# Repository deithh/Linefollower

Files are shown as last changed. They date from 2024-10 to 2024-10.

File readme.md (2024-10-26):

# Line Follower Robot  

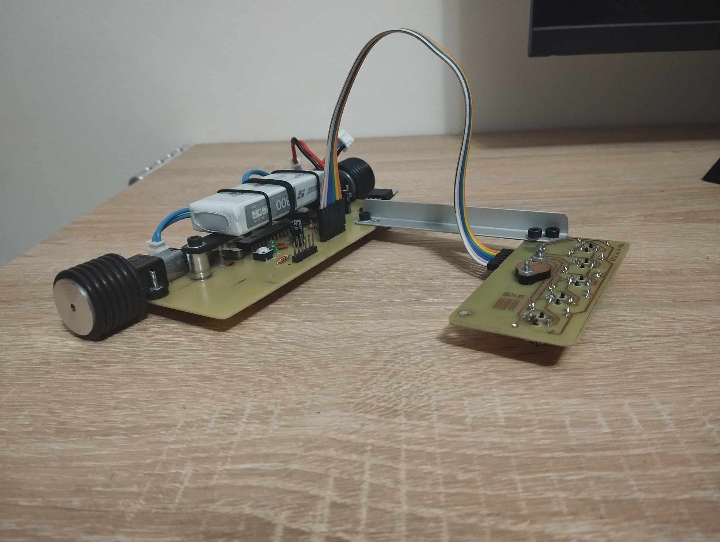
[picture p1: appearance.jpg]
appearance
  

## Overview  
This repository contains the project of a Line Follower Robot developed as part of the Computer Systems Architecture course at the Poznan University of Technology. The robot is designed to autonomously follow a black line on a flat surface using embedded sensors and self-developed control logic. The project involved designing, assembling, and programming the robot from scratch.  

**We managed to create an autonomous system that can follow the line at a speed of approximately 0.6 m/s**  
We won a competition outperforming 10 other teams with our creation of a lightweight robot featuring an efficient drive system.  

## Team Members  
1. Hubert Błaszczyk - 155085
- PCB etching
- Software development
- Video production
- System testing and calibration

2. Bartosz Operacz - 155957
- PCB etching
- Software development
- Documentation preparation
- System testing and calibration

3. **I was responible for:**
- PCB etching
- Robot design
- Component assembly
- System testing and calibration  

## Project Goal
The objective of the project was to develop a robot capable of autonomously tracking a black line by:

- Detecting a black line beneath it  
- Operating on a flat surface with the ability to steer and adjust speed  
- Being self-powered  
- Generating signals to follow the line accurately  
- Indicating correct operation through LEDs  
- Allowing easy reprogramming for improvements or troubleshooting  

## Technical Specifications
- Sensors: 5 TCRT5000 optical sensors to detect line position.
- Motors: 2 N20-BT16 motors with 2000 rpm, allowing ~2 m/s speed.
- Motor Driver: TB6612FNG for dual-channel motor control.
- Power Source: 2S 7.4V Li-Pol battery.
- Voltage Regulator: LM7805 with reverse current protection.
- Microcontroller: ATMEGA328P-PN, 16MHz clock.
- Other Features: Custom PCB with solder mask, LED indicators, programmable SPI interface.

## Software Overview
The software was developed to:  

Read sensor signals to determine the robot's position relative to the line.
Control motor speed and direction based on a PID (Proportional-Integral-Derivative) controller.
Use LEDs to signal operational status and low battery levels.
Key Functions:

drive_motors: Controls motor speed and direction.
calibrate: Calibrates the sensors for line detection.
calculate_error: Calculates deviation from the line.
PID control: Adjusts motor speed to correct positioning.
Assembly and Etching
The PCB etching process was completed in-house, following these steps:

Preparing film layouts.
UV exposure and etching.
Drilling and mounting components.
Final soldering and assembly.

## Budget Summary
The total cost for the project components was approximately 404.53 PLN.

## Demo Video
A video demonstration of the Line Follower Robot is available on YouTube:  
[result](https://youtu.be/YW8YQgWOzjk)  
[project video](https://www.youtube.com/watch?v=wPkWPQ8s4SI&ab_channel=NapewnonieHubert)  

## Notes
Capacitor C5 was removed due to programming issues.  
The footprint for LM7805 was incorrectly sized, requiring adjustments.

### Project documentation is available in polish

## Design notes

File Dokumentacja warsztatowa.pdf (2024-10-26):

INSTYTUT INFORMATYKI
WYDZIAL INFORMATYKI I TELEKOMUNIKACJI, POLITECHNIKA POZNANSKA

## ARCHITEKTURA SYSTEMÓW KOMPUTEROWYCH 2024

prowadzący: dr inż. RAFAŁ KLAUS

## Line Follower

### drużyna warsztatowa nr 8

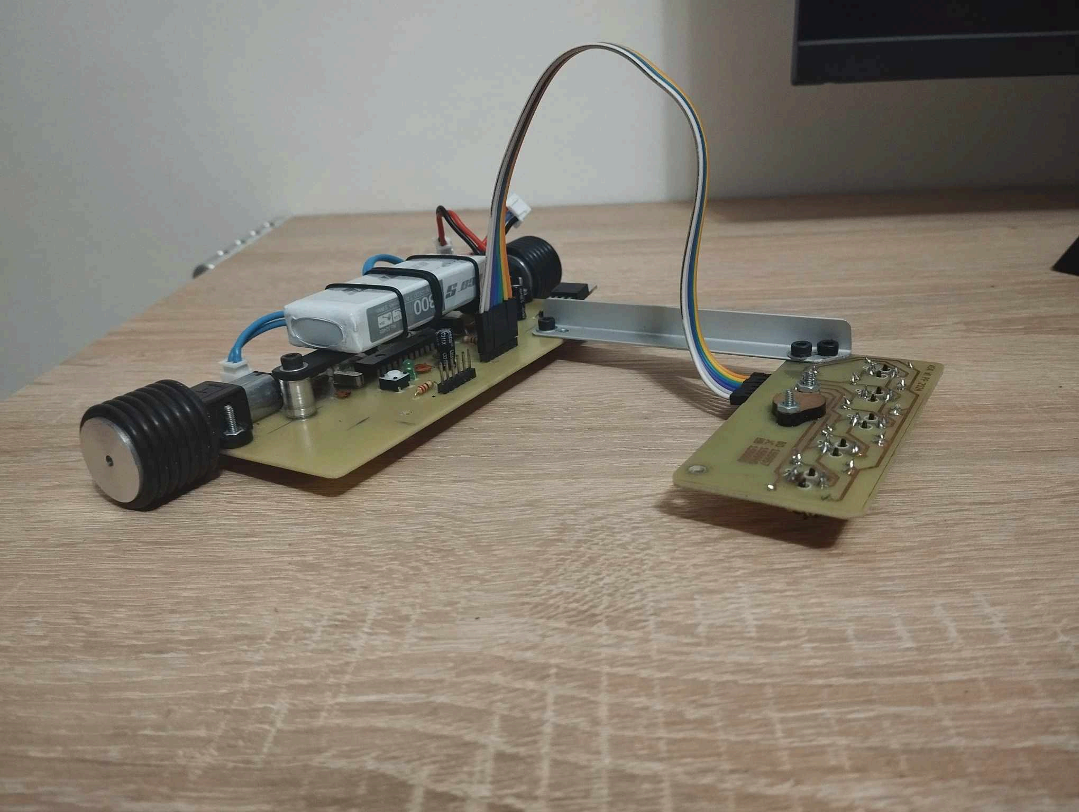
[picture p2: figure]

Lp. | Autorzy | Indeks | nr grupy dziekańskiej | Zadania
1 | Hubert Błaszczyk | 155085 | 6 | 1. Wytrawienie płyt 2. Realizacja oprogramowania 3. Wykonanie filmu 4. Testowanie i trymowanie systemu
2 | Jan Cieśla | 155945 | 4 | 1. Wytrawienie płyt 2. Projekt robota 3. Montaż komponentów 4. Testowanie i trymowanie systemu
3 | Bartosz Operacz | 155957 | 1 | 1. Wytrawienie płyt 2. Realizacja oprogramowania 3. Przygotowanie dokumentacji 4. Testowanie i trymowanie systemu

Poznań, 2024

# Wprowadzenie

Celem naszej drużyny było własnoręczne stworzenie robota typu LineFollower, którego zadaniem jest podążanie po znajdującej się na podłodze czarnej linii.
Pomysł zakłada że robot powinien:
- wykrywać znajdującą się pod nim linię,
- mieć możliwość poruszania się po płaskiej powierzchni, skręcania
- posiadać własne zasilanie,
- generować odpowiednie sygnały umożliwiające podążanie za linią,
- móc informować o jego prawidłowym funkcjonowaniu,
- mieć możliwość łatwego programowania z zewnątrz.

# Rozwiązania techniczne

W robocie zastosowano:
- 5 transoptorów odbiciowych TCRT5000 aby wykrywać czarną linię. Zastosowane ze względu na wysoki dystans działania.
- 2 silniki N20-BT16 służące za napęd, połączone bezpośrednio do kół robota pozbywając się w ten sposób problemów związanych z przenoszeniem napędu, jednocześnie realizując skręt. 2000 rpm pozwala na jazdę z prędkością ok 2m/s przy zastosowanych przez nas kołach fi24mm, zapewniając zadowalające przyspieszenie.
- dwukanałowy sterownik silników TB6612FNG umożliwiający sterowanie silnikami,
- pakiet Li-Pol 2S 7.4V 20C Dualsky 800mAh - zasilanie robota. Dobrane ze względu na dobry stosunek wagi do pojemności oraz możliwość dostarczenia prądu o dużym natężeniu.
- stabilizator napięcia LM7805 wraz z układem zabezpieczenia przed prądem zwrotnym,
- mikrokontroler ATMEGA328P-PN taktowany oscylatorem 16MHz,
- dzielnik napięcia aby umożliwić pomiar napięcia pakietu i wykrycie gdy jest on zbyt niski,
- 2 diody led oraz przycisk w celu umożliwienia komunikacji człowiek-robot,
- wyprowadzony interfejs spi służący do programowania robota.
- zabezpieczenie przed odwrotnym podłączeniem zasilania w postaci asymetrycznego gniazda zasilania
- Filtracja zasilania dla układów scalonych, układ zaprojektowany z troską o minimalizację zakłóceń

## Opis konstrukcji robota

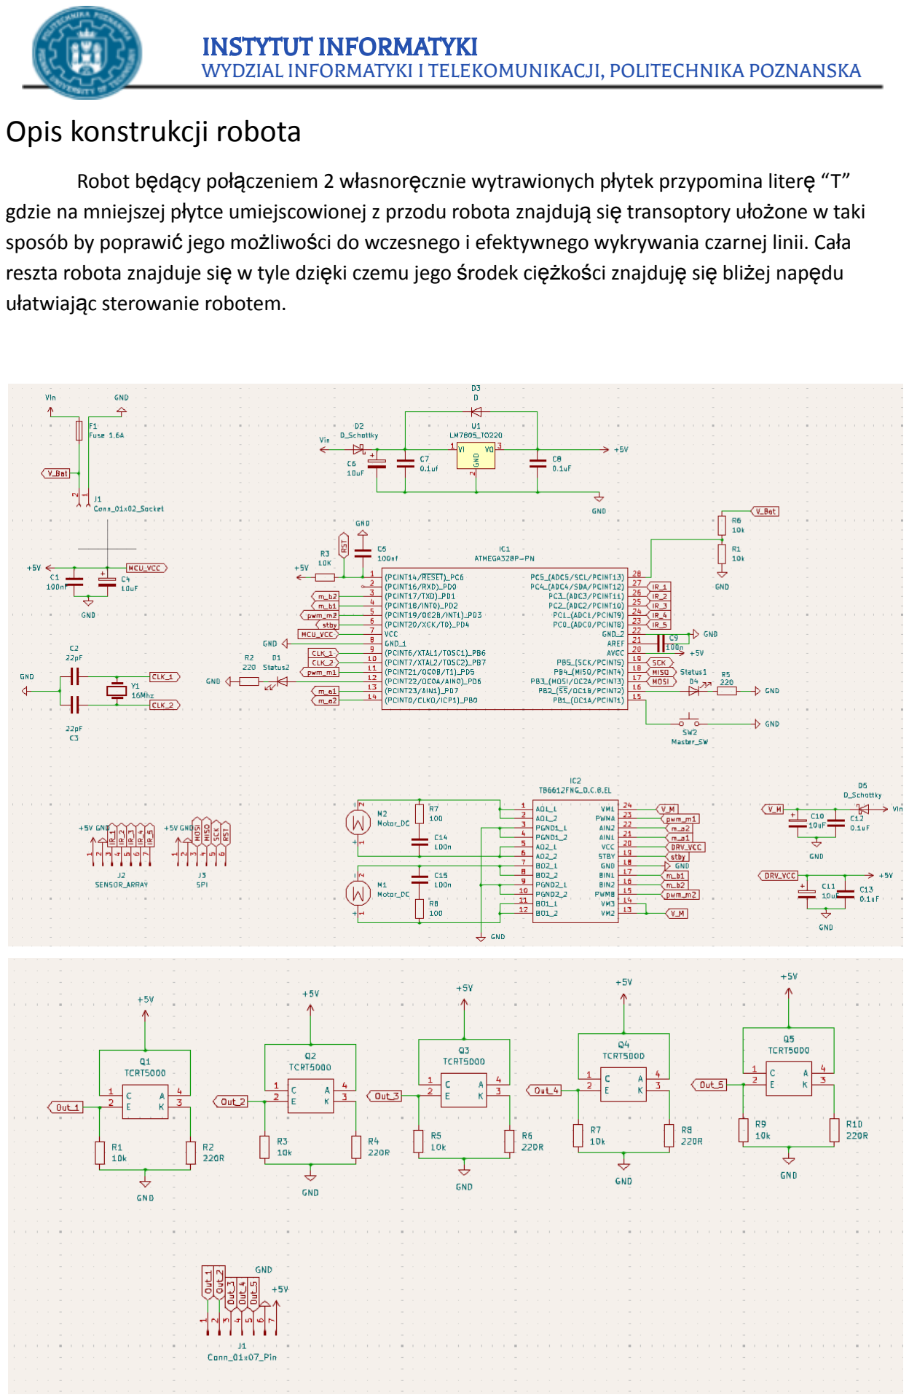
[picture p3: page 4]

Robot będący połączeniem 2 własnoręcznie wytrawionych płytek przypomina literę “T” gdzie na mniejszej płytce umiejscowionej z przodu robota znajdują się transoptory ułożone w taki sposób by poprawić jego możliwości do wczesnego i efektywnego wykrywania czarnej linii. Cała reszta robota znajduje się w tyle dzięki czemu jego środek ciężkości znajduję się bliżej napędu ułatwiając sterowanie robotem.

# Schematy i opis

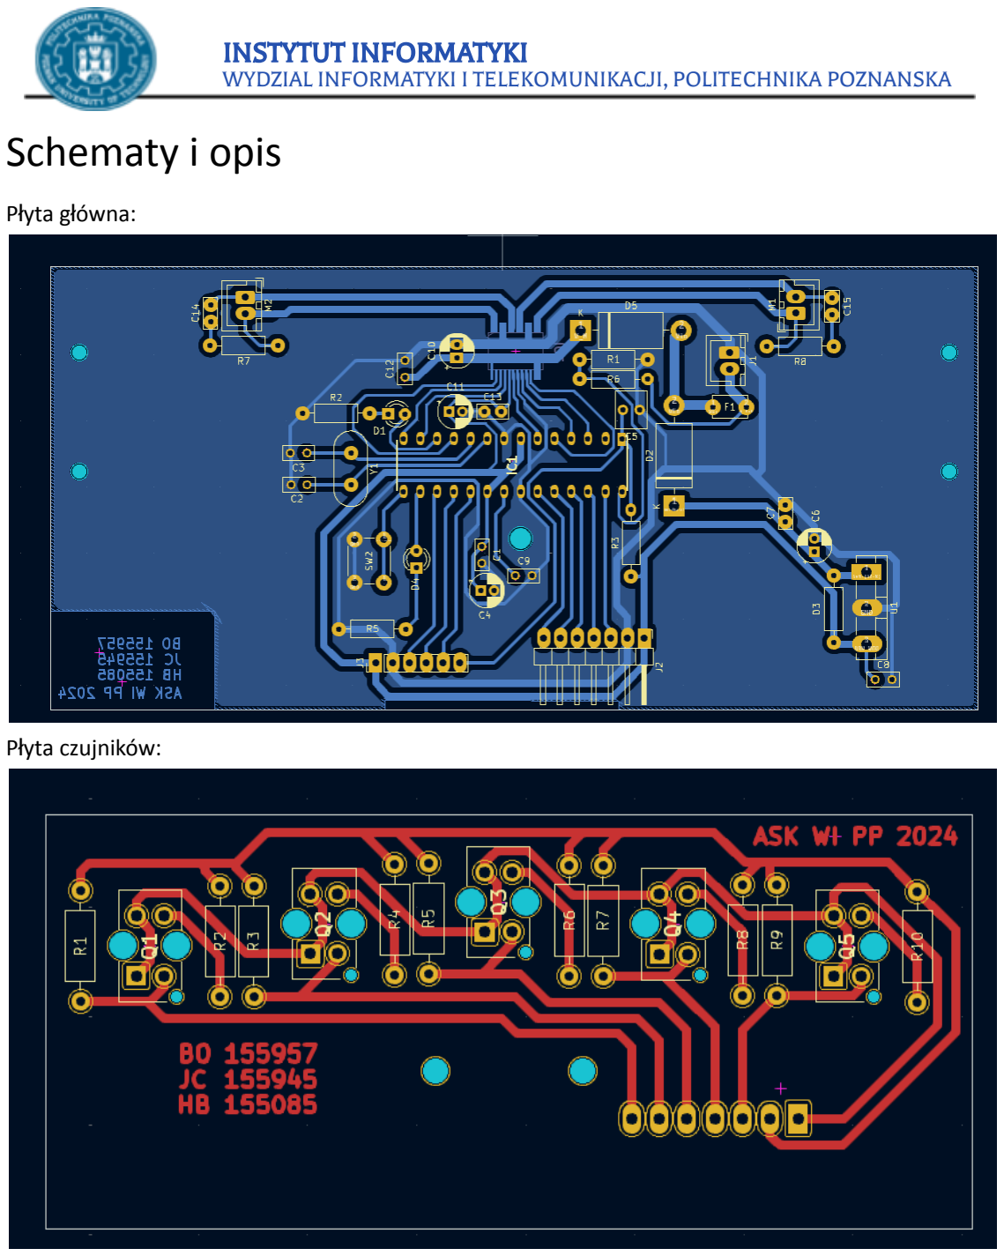
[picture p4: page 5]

Płyta główna:

Płyta czujników:

## Opis trawienia:

- Przygotowanie klisz - wydruk layout’u na kalce technicznej lub przezroczystej folii. W celu ograniczenia transparentności klisz połączyliśmy dwie naraz, wymagane jest precyzyjne ustawienie z pomocą znaków ustalających na wydrukach.
- Przygotowanie ciemni (żółte / czerwone światło), roztworów wywoływacza uniwersalnego w proporcji 5.5g/100ml i nadsiarczanu sodu 20g/100ml oraz laminatu z fotorezystem pozytywowym dociętym ok 5mm nad wymiar, należy ogratować krawędzie laminatu. Wywoływacz w temperaturze pokojowej, wytrawiacz należy podgrzać w kąpieli wodnej do ok 50 stopni.
- Zdjęcie folii ochronnej z laminatu, ustawienie kliszy (klisza nie odbita lustrzanie, tonerem do laminatu).
- Naświetlenie płyty światłem UV przez eksperymentalnie dobrany czas (w naszym przypadku 180s). Należy zwrócić uwagę na notę katalogową laminatu i długość fali emitowaną przez naszą lampe, w naszym przypadku duża lampa do paznokci spełniła swoje zadanie. Podczas naświetlania wymagany jest docisk kliszy do laminatu aby uniknąć wybrzuszania się kliszy. (Do przygotowania małego PCB wystarczyła nam ciężka szyba, w przypadku płyty głównej posłużyliśmy się workiem próżniowym i ciśnieniem atmosfery)
- Wywoływanie ok 150-180s w roztworze o temperaturze pokojowej, wymagane mieszanie. Po wyjęciu płytkę należy wypłukać. Za krótko wywoływany rezyst nie dopuści do poprawnego wytrawiania się PCB.
- Wytrawianie ok 10-20min w zależności od rozmiaru płyty i świeżości roztworu, wymagane utrzymywanie b327 w podwyższonej temperaturze. Trawimy do momentu zaniku 100% miedzi z przestrzeni między ścieżkami. Po wyjęciu płytkę należy wypłukać.
- Zmycie pozostałego rezystu acetonem, obcięcie nadwymiarowego laminatu piłą włośnicową.
- Zabezpieczenie PCB lakierem / soldermaską.

# Oprogramowanie

W celu zapewnienia odpowiedniego sposobu działania robota wymagane było napisanie oprogramowania, którego zadaniem było odczytywanie wartości sygnałów zwracanych przez transoptory odbiciowe i na ich podstawie generowanie odpowiednich sygnałów do sterownika silników aby robot poruszał się zgodnie z czarną linią.

## Wykorzystane biblioteki

W programie skorzystano z biblioteki TB6612 SparkFun ułatwiającej sterowanie silnikami.

Znajdujące się w niej klasa, metody, i procedury, które zostały użyte w programie to:
- klasa Motor

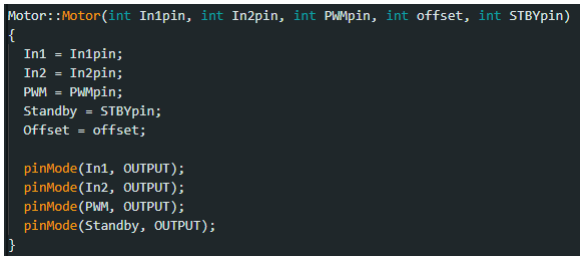
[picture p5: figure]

- drive (wykorzystywana do poruszania konkretnym silnikiem)

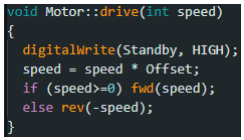
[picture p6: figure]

- fwd

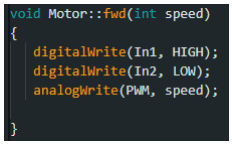
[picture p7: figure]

- rev

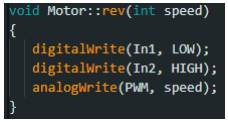
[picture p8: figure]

- procedura brake (wykorzystywana do hamowania obu silników)
- metoda brake

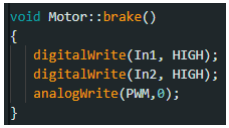
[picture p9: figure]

## Zdefiniowane stałe

Dla ułatwienia i zwiększenia czytelności zdefiniowano makra zastępujące identyfikatory odpowiednimi numerami pinów i innych pomocniczych stałych.

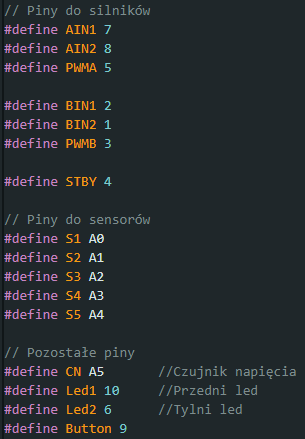
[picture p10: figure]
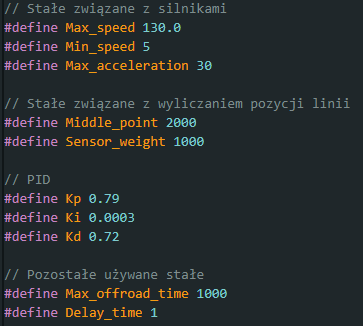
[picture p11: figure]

## Wykorzystane funkcje

Na potrzeby programu zdefiniowano kilka makr, procedur i funkcji pomocniczych:
- sbi i cbi (wykorzystywane do ustawiania konkretnych bitów rejestrów sfr)

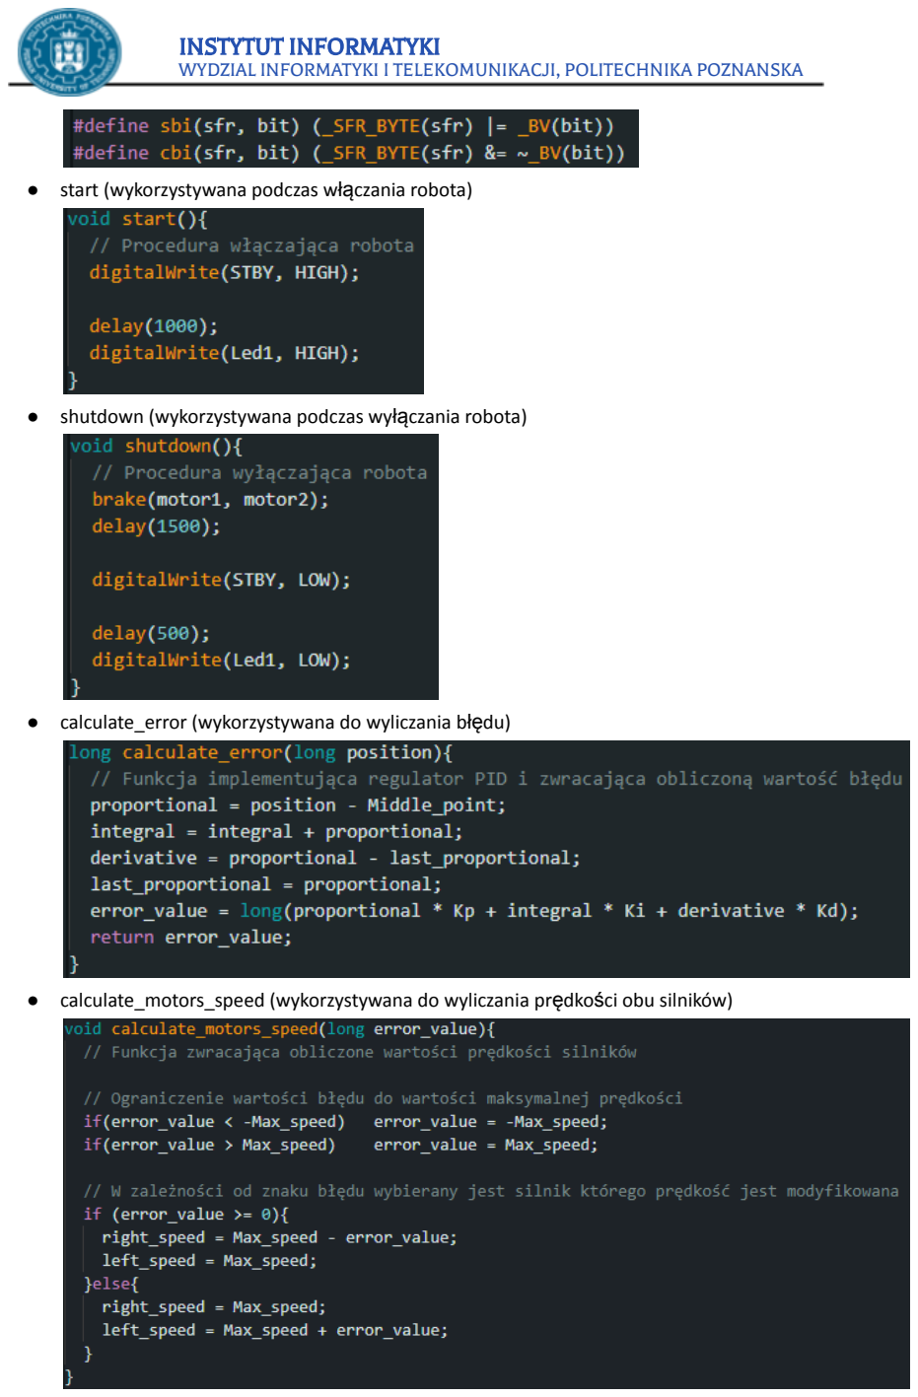
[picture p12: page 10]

- start (wykorzystywana podczas włączania robota)
- shutdown (wykorzystywana podczas wyłączania robota)
- calculate_error (wykorzystywana do wyliczania błędu)
- calculate_motors_speed (wykorzystywana do wyliczania prędkości obu silników)

- drive_motors (wykorzystywana do sterowania silnikami)

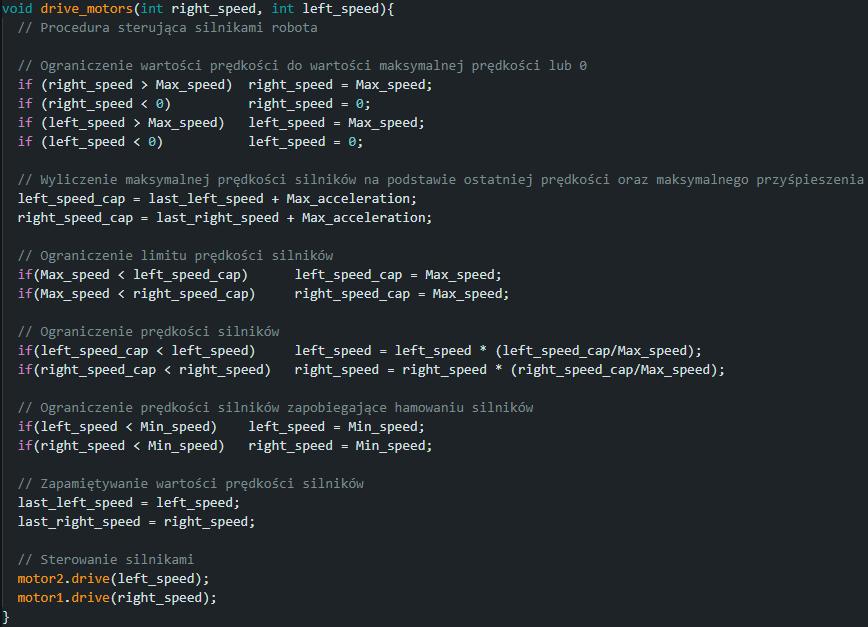
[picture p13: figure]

- calibrate (wykorzystywana do kalibracji sensorów)

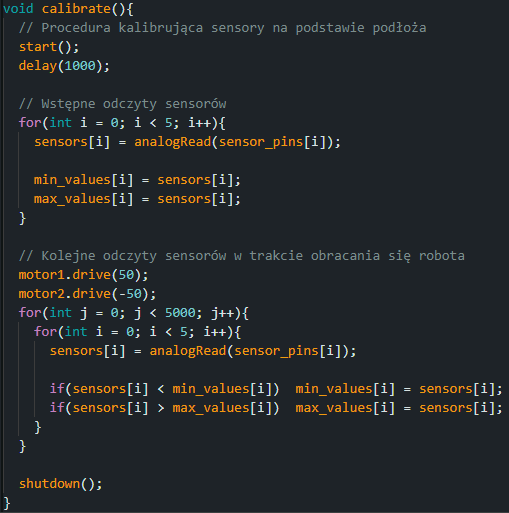
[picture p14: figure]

## Deklaracja i inicjalizacja zmiennych

Na początku programu są deklarowane i inicjalizowane wszystkie zmienne wymagane do poprawnego działania programu.

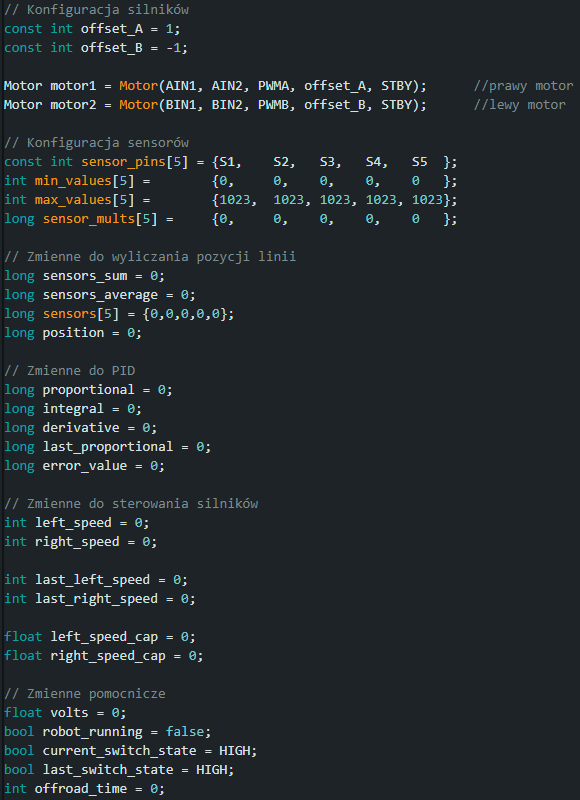
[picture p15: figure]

## Przygotowanie mikrokontrolera do działania

Następnie dokonywana jest:
- konfiguracja,

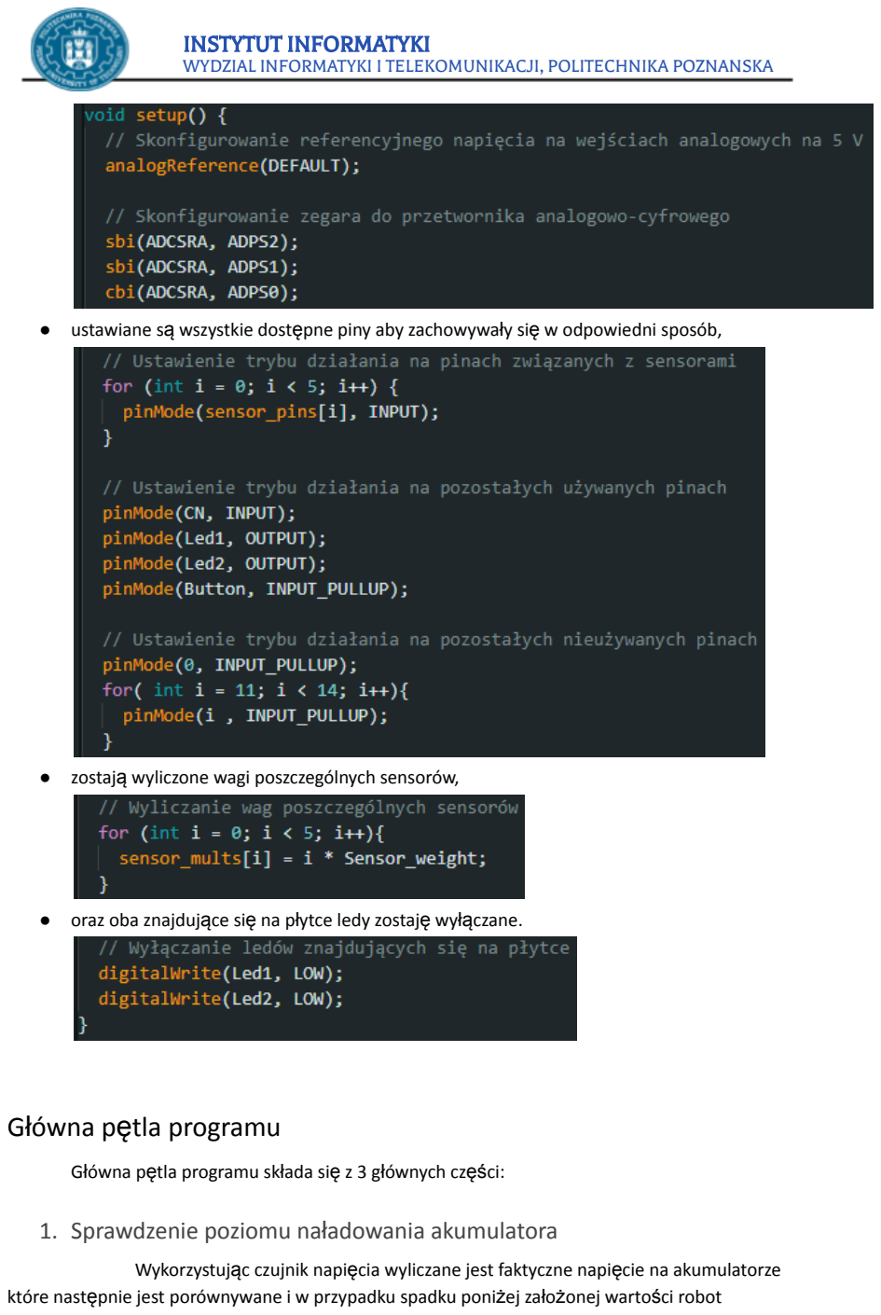
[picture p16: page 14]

- ustawiane są wszystkie dostępne piny aby zachowywały się w odpowiedni sposób,
- zostają wyliczone wagi poszczególnych sensorów,
- oraz oba znajdujące się na płytce ledy zostaję wyłączane.

## Główna pętla programu

Główna pętla programu składa się z 3 głównych części:

### 1. Sprawdzenie poziomu naładowania akumulatora

Wykorzystując czujnik napięcia wyliczane jest faktyczne napięcie na akumulatorze które następnie jest porównywane i w przypadku spadku poniżej założonej wartości robot odpowiednio informuje zapalając odpowiednią diodę, lub w przypadku jeszcze większego odchyłu napięcia program zatrzyma działanie i nie pozwoli na ponowne uruchomienie robota jednocześnie informując o krytycznym poziomie akumulatora migającą diodą led.

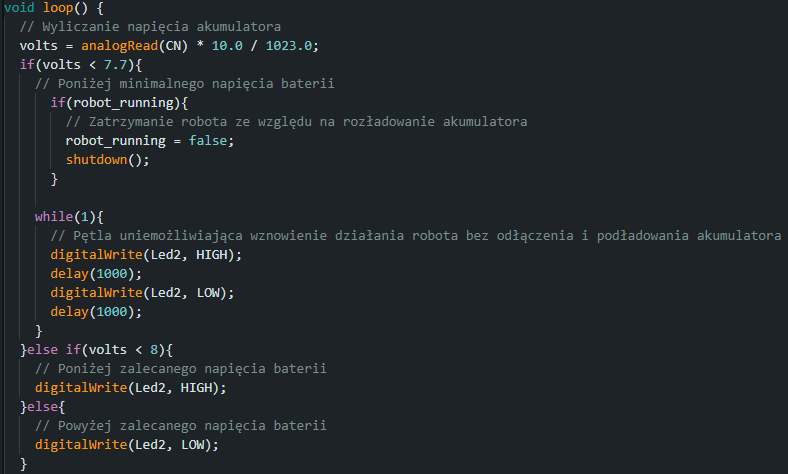
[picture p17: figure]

### 2. Sekcja związana z przyciskiem

Za pomocą zmiennej przechowującej ostatni stan przycisku jest możliwe wyłapanie przez program momentu jednokrotnego naciśnięcia przycisku a przez powtórne sprawdzenie stanu przycisku możliwe jest rozróżnienie krótszego i dłuższego przytrzymania przycisku dzięki czemu można wybrać czy robot powinien zacząć kalibrację lub odpowiednio zostać włączony lub wyłączony zależnie od jego aktualnego stanu (w trakcie działania robota kalibracja jest niemożliwa). O aktualnym stanie robota informuje dioda led umieszczona w tylnej części robota.

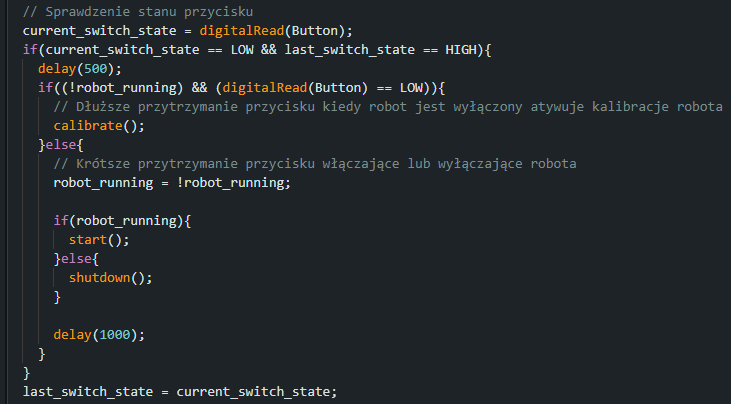
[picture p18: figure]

### 3. Sekcja związana z jazdą po linii

Jeżeli robot został włączony przez naciśnięcie przycisku to zaczyna odczytywać wartości z sensorów, które następnie są wykorzystywane do określenia pozycji czarnej linii. Znając pozycję można przystąpić do wyliczanie błędu czyli wartości wskazującej na to jak mocno i w którą stronę należy skręcić aby pozostać na linii. Do wyliczenia tej wartości zastosowano regulator PID. Mając wyliczony błąd można następnie wykorzystać go do obliczenia prędkości silników i następnie odpowiednio wysterować silniki.
Zanim zostaje obliczona pozycja linii następuje sprawdzenie czy robot faktycznie znajduję się w miejscu w którym mógłby śledzić linię. Jeżeli tak nie jest to zamiast wyliczenia nowych prędkości silników, robot porusza się w ten sam sposób jak w ostatniej iteracji oraz jest zwiększana zmienna oznaczająca czas poza trasą a w momencie kiedy przekroczy ona dopuszczalną wartość, robot zostaje automatycznie wyłączony.

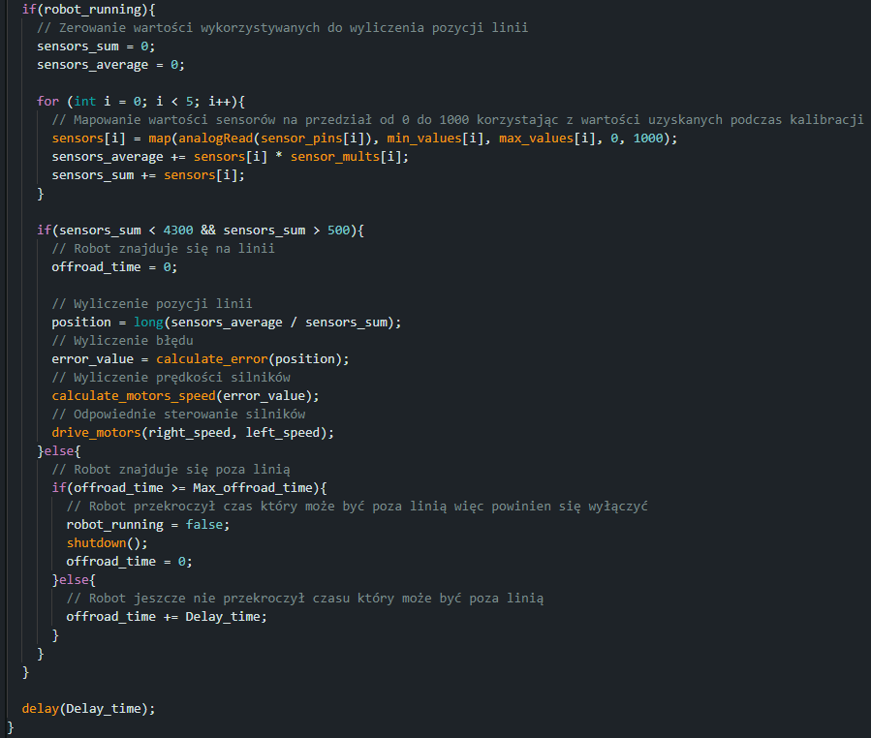
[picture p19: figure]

# Kosztorys

Nazwa | Iloś ć | Cena | Łącznie | Link

BOTLAND

silnik dc | 2 | 25.90 | 51.80 | link (https://botland.com.pl/silniki-micro-n20-seria-mp-medium-power/12592-silnik-n20-bt33-micro-2501-50rpm-9v-5904422319717.html)
wytrawiacz | 1 | 6.50 | 6.50 | link (https://botland.com.pl/wytrawiacze-miedzi/1057-wytrawiacz-b327-100g-5901764329183.html)
wywoływacz | 1 | 3.50 | 3.50 | link (https://botland.com.pl/wytrawiacze-miedzi/5697-uniwersalny-wywolywacz-do-fotolakierow-i-laminatow-pozytywowych-22g-5901764329305.html)
mocowania do silników | 2 | 6.95 | 13.90 | link (https://botland.com.pl/mocowania-silnikow/25-mocowania-do-micro-silnikow-pololu-biale-2szt-pololu-1086-5904422300272.html)
nakrętki opakowanie | 1 | 3.90 | 3.90 | link (https://botland.com.pl/srubki-i-nakretki/806-nakretki-m3-10szt-5904422300982.html)
śrubki, nakrętki opakowanie | 2 | 1.40 | 2.80 | link (https://botland.com.pl/srubki-i-nakretki/7804-srubki-m3-6mm-podkladki-10szt-5904422310745.html)
wiertło (1 mm) | 10 | 0.50 | 5.00 | link (https://botland.com.pl/wiertla/234-wiertlo-10mm-10szt-5906083201004.html)
wiertło 0,7mm | 10 | 0.95 | 9.50 | link (https://botland.com.pl/wiertla/232-wiertlo-07mm-10szt-5904422372163.html)

Nazwa | Iloś ć | Cena | Łącznie | Link
kondensator 10uf spolaryzowany | 20 | 0.10 | 2.00 | link (https://botland.com.pl/kondensatory-elektrolityczne-tht/211-kondensator-elektrolityczny-10uf-50v-5x11mm-105c-tht-10szt-5903351248259.html)
kondensator 22pf | 10 | 0.10 | 1.00 | link (https://botland.com.pl/kondensatory-ceramiczne-tht/448-kondensator-ceramiczny-22pf-50v-tht-10-szt-5904422355609.html)
pakiet lipo 2s | 2 | 34.90 | 69.80 | link (https://botland.com.pl/akumulatory-li-pol-2s-74v-/2393-pakiet-li-pol-dualsky-800mah-25c-2s-74v-eco-s-6941047104655.html)
kondensator 100nF | 10 | 0.10 | 1.00 | link (https://botland.com.pl/kondensatory-ceramiczne-tht/210-kondensator-ceramiczny-100nf50v-tht-10szt-5903351248198.html)
kulka ball caster | 1 | 13.00 | 13.00 | link (https://botland.com.pl/kulki-podporowe/63-ball-caster-38-metalowy-pololu-951-5904422362690.html)
przewody zestaw | 1 | 6.50 | 6.50 | link (https://botland.com.pl/przewody-polaczeniowe-zensko-zenskie/19620-zestaw-przewodow-polaczeniowych-justpi-zensko-zenskie-20cm-40szt-5903351243032.html)
rezystor 10k 5% | 10 | 0.19 | 1.90 | link (https://botland.com.pl/rezystory-przewlekane/20150-rezystor-justpi-tht-cf-weglowy-14w-10k-30szt-5904422329280.html)
rezystor 220R 5% | 10 | 0.19 | 1.90 | link (https://botland.com.pl/rezystory-przewlekane/20014-rezystor-justpi-tht-cf-weglowy-14w-220-30szt-5904422329020.html)
cyna | 1 | 6.90 | 6.90 | link (https://botland.com.pl/cyny-i-pasty-lutownicze/309-cyna-w-fiolce-16g-100mm-5902884600091.html)
plecionka | 1 | 5.90 | 5.90 | link (https://botland.com.pl/odsysacze-i-plecionki/757-plecionka-do-odsysania-cyny-1mm-5904422358969.html)
topnik | 1 | 4.70 | 4.70 | link (https://botland.com.pl/kalafonie-i-topniki/433-topnik-rf800-15ml-5901764320241.html)
kondensator 100uf | 15 | 0.15 | 2.25 | link (https://botland.com.pl/kondensatory-elektrolityczne-tht/898-kondensator-elektrolityczny-100uf-35v-6x12mm-105c-tht-10szt-5903351248235.html)
dioda led | 1 | 1.90 | 1.90 | link (https://botland.com.pl/diody-led/19987-dioda-led-3mm-zielona-10szt-justpi-5904422328757.html)
Rezonator kwarcowy 16MHz | 3 | 0.70 | 2.10 | link (https://botland.com.pl/rezonatory/166-rezonator-kwarcowy-16mhz-hc49-niski-5904422358761.html)

TME

sterownik silników toshiba tb6612fng | 1 | 11.37 | 11.37 | link (https://www.tme.eu/pl/details/tb6612fng/drivery-silnikowe-i-pwm/toshiba/tb6612fng-o-c-8-el/)
mikrokontroler ATmega328p-pn | 1 | 15.77 | 15.77 | link (https://www.tme.eu/pl/details/atmega328p-pn/rodzina-avr-8-bit/microchip-technology/)
laminat | 1 | 26.08 | 26.08 | link (https://www.tme.eu/pl/details/fr4150x200_3500/laminaty-jednostronne/bungard/120306e38/)
transoptor odbiciowy TCRT5000 | 5 | 5.01 | 25.05 | link (https://www.tme.eu/pl/details/tcrt5000/czujniki-fotoelektryczne-do-druku/vishay/)
stabilizator napięcia LM7805 | 1 | 8.50 | 8.50 | link (https://www.tme.eu/pl/details/lm7805ct_nopb/stabilizatory-napiecia-nieregulowane-ldo/texas-instruments/)
Dioda 1n5822RL shottky | 5 | 0.88 | 4.40 | link (https://www.tme.eu/pl/details/1n5822rl-st/diody-schottky-tht/stmicroelectronics/1n5822rl/)
koła - o-ring 17x3 | 20 | 0.39 | 7.80 | link (https://www.tme.eu/pl/details/o-17x3-70-nbr/uszczelki/oring-uszczelnienia-techniczne/01-0017-00x-3-oring-70nbr/)
mikroprzełącznik | 4 | 0.79 | 3.16 | link (https://www.tme.eu/pl/details/1825910-2/mikroprzelaczniki-tact/te-connectivity/)
styk jst | 20 | 0.37 | 7.40 | link (https://www.tme.eu/pl/details/sxh-001t-p0.6/zlacza-sygnalowe-raster-2-50mm/jst/)
bezpiecznik polimerowy 1.6A | 3 | 1.45 | 4.35 | link (https://www.tme.eu/pl/details/rb160-30/bezpieczniki-polimerowe-tht/ece/)
gniazdo jst xh | 10 | 0.62 | 6.20 | link (https://www.tme.eu/pl/details/b2b-xh-a/zlacza-sygnalowe-raster-2-50mm/jst/b2b-xh-a-lf-sn/)
wtyk jst xh | 10 | 0.37 | 3.70 | link (https://www.tme.eu/pl/details/xhp-2/zlacza-sygnalowe-raster-2-50mm/jst/)

INNE

wiertło 3mm | 2 | 3.00 | 6.00 | -
taśma izolacyjna | 1 | 8.00 | 8.00 | -
brzeszczot | 2 | 5.00 | 10.00 | -

Nazwa | Iloś ć | Cena | Łącznie | Link
papier ścierny p120 | 1 | 2.00 | 2.00 | -
papier ścierny p1000 | 1 | 2.00 | 2.00 | -
kątownik aluminiowy | 1 | 10.00 | 10.00 | -
wydruki | 3 | 4.00 | 12.00 | -
aceton | 1 | 5.00 | 5.00 | -
worek próżniowy | 1 | 8.00 | 8.00 | -

ZAPASY DOMOWE

koła - wałek aluminiowy fi20 | 1 | 0.00 | 0.00 | -
dioda 1n4007 | 1 | 0.00 | 0.00 | -
rezystor 10k 1% | 2 | 0.00 | 0.00 | -
rezystor 100R 1% | 2 | 0.00 | 0.00 | -
rezystor 4.7k 5% | 2 | 0.00 | 0.00 | -
wiertło 1.5mm | 1 | 0.00 | 0.00 | -
wiertło 3.2mm | 1 | 0.00 | 0.00 | -
kołki mocujące - wałek aluminiowy fi15 | 1 | 0.00 | 0.00 | -
płaskownik węglowy | 1 | 0.00 | 0.00 | -
Całkowita suma: | | | 404.53

# Film

Link do filmu na youtube:
ASKs 8 - Line Follower (https://youtu.be/wPkWPQ8s4SI)

# Inne uwagi

- Kondensator C5 został źle dobrany i finalnie został zdemontowany (uniemożliwiał programowanie mikrokontrolera, za wysoka pojemność uniemożliwia pojawienie się stanu niskiego na pinie RST w odpowiednim czasie. Jego brak nie wpływa negatywnie na działanie systemu. Podczas projektowania został dodany ze względu na obawę przed zakłóceniami spowodowanymi obciążeniem indukcyjnym.
- Błędnie dobrany footprint LM7805
- Montaż układu w obudowie SSOP24 wymagał wysokiej precyzji wykonania PCB. Z tego względu zdecydowaliśmy się na technologię fotochemiczną

- Układ stabilizatora LM7805 powinien być zastąpiony stabilizatorem typu LDO, znacznie wydłużyłoby to czas działania układu na zasilaniu akumulatorowym
- Silniki n20 wykazują się niską jakością wykonania, podczas testowania jeden z użytych wymagał wymiany szczotki.
- uchwyt wiertarski dla wierteł od 1.5mm jest w stanie “złapać” wiertło 0.7mm pogrubione opaską termokurczliwą, jednak obniża to jakość wiercenia
- korzystając z wyższych taktowań zegara wymagane jest obniżenie taktowania przetwornika adc w celu zachowania dokładności.

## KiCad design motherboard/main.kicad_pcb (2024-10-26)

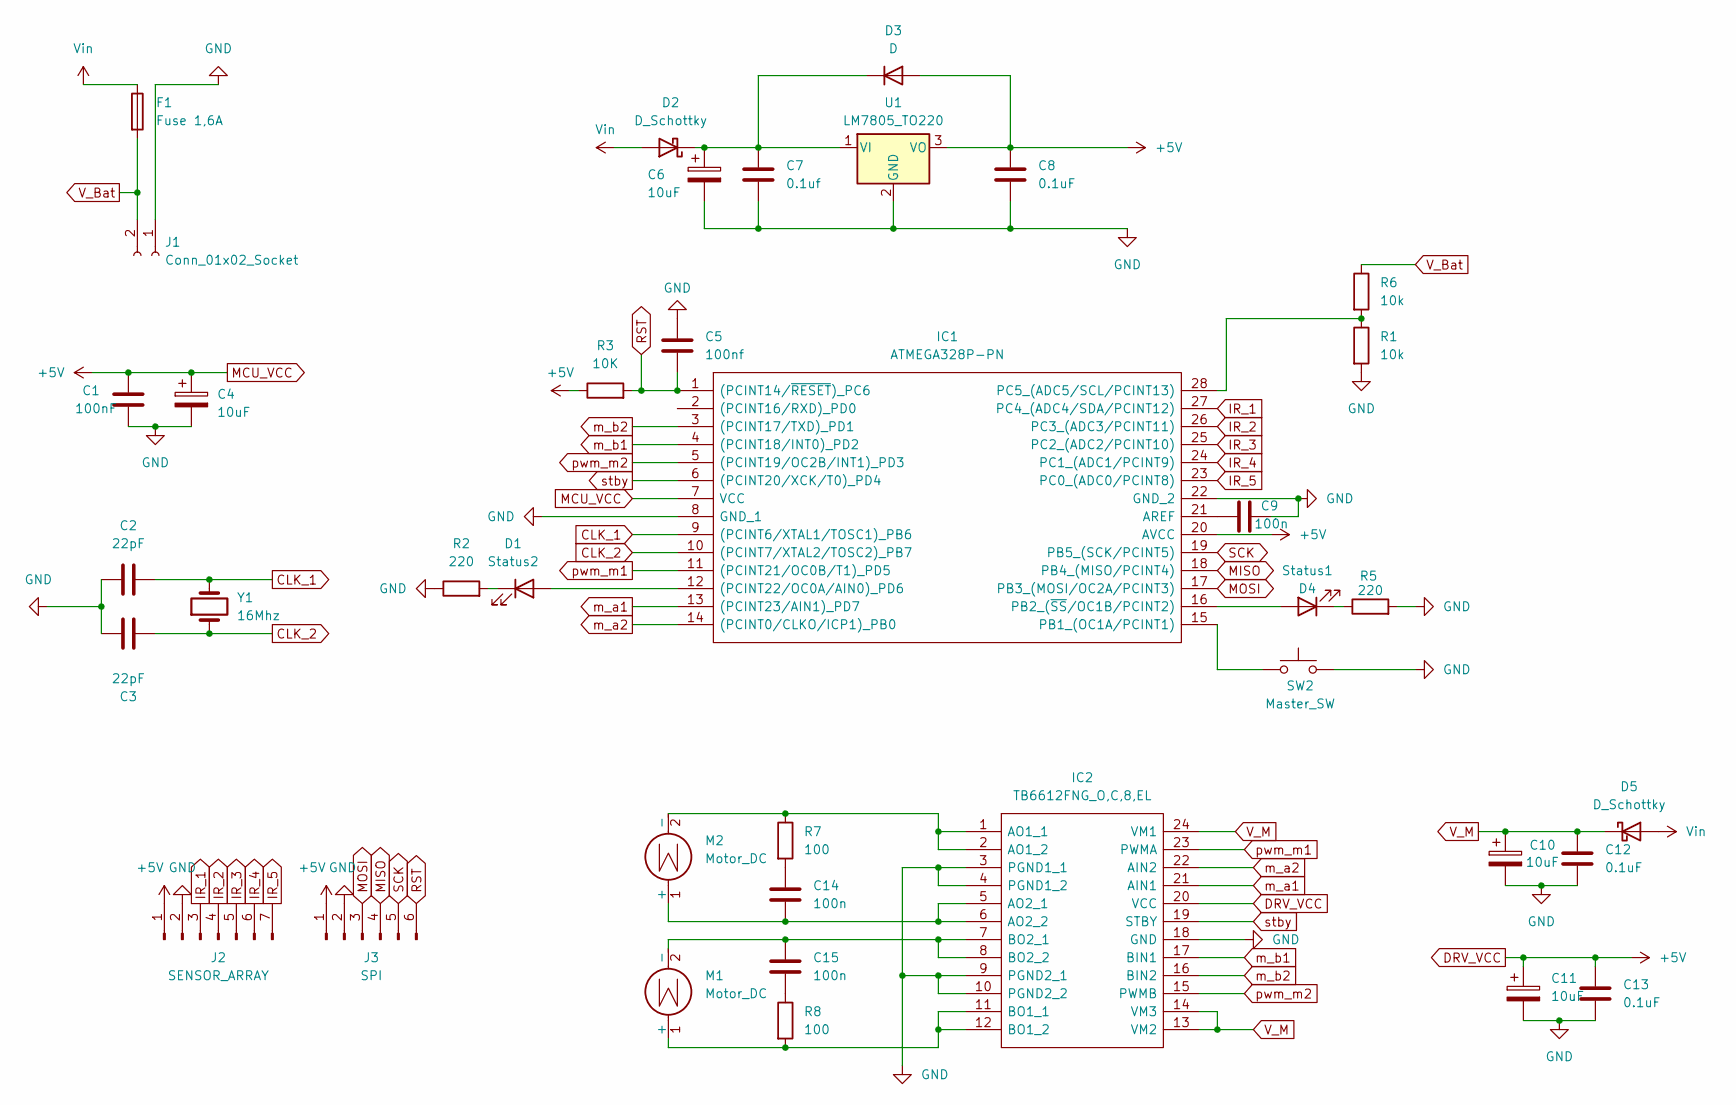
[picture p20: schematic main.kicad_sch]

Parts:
C1: 100nF; C_Rect_L4.6mm_W2.0mm_P2.50mm_MKS02_FKP02
C2, C3: 22pF; C_Rect_L4.6mm_W2.0mm_P2.50mm_MKS02_FKP02
C4, C6, C10, C11: 10uF; CP_Radial_D5.0mm_P2.00mm
C5: 100nf; C_Rect_L4.6mm_W5.5mm_P2.50mm_MKS02_FKP02
C7: 0.1uf; C_Rect_L4.6mm_W2.0mm_P2.50mm_MKS02_FKP02
C8, C12, C13: 0.1uF; C_Rect_L4.6mm_W2.0mm_P2.50mm_MKS02_FKP02
C9, C14, C15: 100n; C_Rect_L4.6mm_W2.0mm_P2.50mm_MKS02_FKP02
D1: Status2; LED_D3.0mm_FlatTop
D2, D5: D_Schottky; D_DO-201AD_P15.24mm_Horizontal
D3: D; R_Axial_DIN0207_L6.3mm_D2.5mm_P10.16mm_Horizontal
D4: Status1; LED_D3.0mm_FlatTop
F1: Fuse 1,6A; C_Disc_D5.1mm_W3.2mm_P5.00mm
IC1: ATMEGA328P-PN; DIP794W53P254L3467H457Q28N; Manufacturer_Part_Number ATMEGA328P-PN
IC2: TB6612FNG_O,C,8,EL; SOP65P760X160-24N; Manufacturer_Part_Number TB6612FNG(O,C,8,EL
J1: Conn_01x02_Socket; JST_XH_B2B-XH-A_1x02_P2.50mm_Vertical
J2: SENSOR_ARRAY; PinHeader_1x07_P2.54mm_Horizontal
J3: SPI; PinHeader_1x06_P2.54mm_Vertical
M1, M2: Motor_DC; JST_XH_B2B-XH-A_1x02_P2.50mm_Vertical
R1, R6: 10k; R_Axial_DIN0207_L6.3mm_D2.5mm_P10.16mm_Horizontal
R2, R5: 220; R_Axial_DIN0207_L6.3mm_D2.5mm_P10.16mm_Horizontal
R3: 10K; R_Axial_DIN0207_L6.3mm_D2.5mm_P10.16mm_Horizontal
R7, R8: 100; R_Axial_DIN0207_L6.3mm_D2.5mm_P10.16mm_Horizontal
SW2: Master_SW; SW_PUSH_6mm_H4.3mm
U1: LM7805_TO220; TO-3P-3_Vertical
Y1: 16Mhz; Crystal_HC49-4H_Vertical

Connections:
CLK_1: C2.2, IC1.9 ((PCINT6/XTAL1/TOSC1)_PB6), Y1.2
CLK_2: C3.1, IC1.10 ((PCINT7/XTAL2/TOSC2)_PB7), Y1.1
DRV_VCC: C1.1, C4.1, C8.1, C11.1, C13.2, D3.2 (A), IC1.7 (VCC), IC1.20 (AVCC), IC2.20 (VCC), J2.1, J3.1, R3.1, U1.3 (VO)
GND: C1.2, C2.1, C3.2, C4.2, C5.1, C6.2, C7.2, C8.2, C9.2, C10.2, C11.2, C12.2, C13.1, IC1.8 (GND_1), IC1.22 (GND_2), IC2.3 (PGND1_1), IC2.4 (PGND1_2), IC2.9 (PGND2_1), IC2.10 (PGND2_2), IC2.18 (GND), J1.1, J2.2, J3.2, R1.2, R2.1, R5.2, SW2.2, U1.2 (GND)
IR_1: IC1.27 (PC4_(ADC4/SDA/PCINT12)), J2.3
IR_2: IC1.26 (PC3_(ADC3/PCINT11)), J2.4
IR_3: IC1.25 (PC2_(ADC2/PCINT10)), J2.5
IR_4: IC1.24 (PC1_(ADC1/PCINT9)), J2.6
IR_5: IC1.23 (PC0_(ADC0/PCINT8)), J2.7
MISO: IC1.18 (PB4_(MISO/PCINT4)), J3.4
MOSI: IC1.17 (PB3_(MOSI/OC2A/PCINT3)), J3.3
unnamed: C14.1, R7.2
unnamed: C15.2, R8.1
unnamed: D1.2 (A), IC1.12 ((PCINT22/OC0A/AIN0)_PD6)
unnamed: D1.1 (K), R2.2
unnamed: C6.1, C7.1, D2.1 (K), D3.1 (K), U1.1 (VI)
unnamed: D4.2 (A), IC1.16 (PB2_(~SS/OC1B/PCINT2))
unnamed: D4.1 (K), R5.1
unnamed: C9.1, IC1.21 (AREF)
unnamed: IC1.15 (PB1_(OC1A/PCINT1)), SW2.1
unnamed: IC1.28 (PC5_(ADC5/SCL/PCINT13)), R1.1, R6.2
unnamed: IC2.1 (AO1_1), IC2.2 (AO1_2), M2.2 (-), R7.1
unnamed: C14.2, IC2.5 (AO2_1), IC2.6 (AO2_2), M2.1 (+)
unnamed: IC2.11 (BO1_1), IC2.12 (BO1_2), M1.1 (+), R8.2
unnamed: C15.1, IC2.7 (BO2_1), IC2.8 (BO2_2), M1.2 (-)
RST: C5.2, IC1.1 ((PCINT14/~RESET)_PC6), J3.6, R3.2
SCK: IC1.19 (PB5_(SCK/PCINT5)), J3.5
V_Bat: F1.2, J1.2, R6.1
V_M: C10.1, C12.1, D5.1 (K), IC2.13 (VM2), IC2.14 (VM3), IC2.24 (VM1)
Vin: D2.2 (A), D5.2 (A), F1.1
m_a1: IC1.13 ((PCINT23/AIN1)_PD7), IC2.21 (AIN1)
m_a2: IC1.14 ((PCINT0/CLKO/ICP1)_PB0), IC2.22 (AIN2)
m_b1: IC1.4 ((PCINT18/INT0)_PD2), IC2.17 (BIN1)
m_b2: IC1.3 ((PCINT17/TXD)_PD1), IC2.16 (BIN2)
pwm_m1: IC1.11 ((PCINT21/OC0B/T1)_PD5), IC2.23 (PWMA)
pwm_m2: IC1.5 ((PCINT19/OC2B/INT1)_PD3), IC2.15 (PWMB)
stby: IC1.6 ((PCINT20/XCK/T0)_PD4), IC2.19 (STBY)

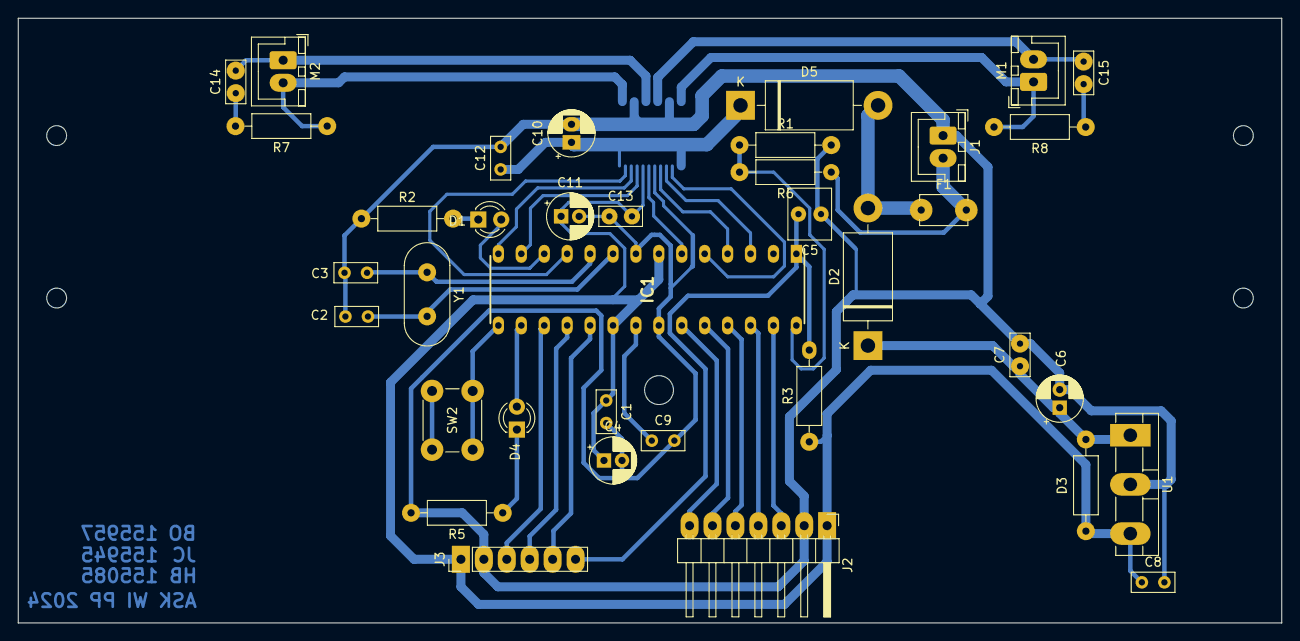
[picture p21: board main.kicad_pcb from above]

Board: 2 copper layers, 140.0 x 67.0 mm, 38 parts (1 on the bottom side), 37 nets.

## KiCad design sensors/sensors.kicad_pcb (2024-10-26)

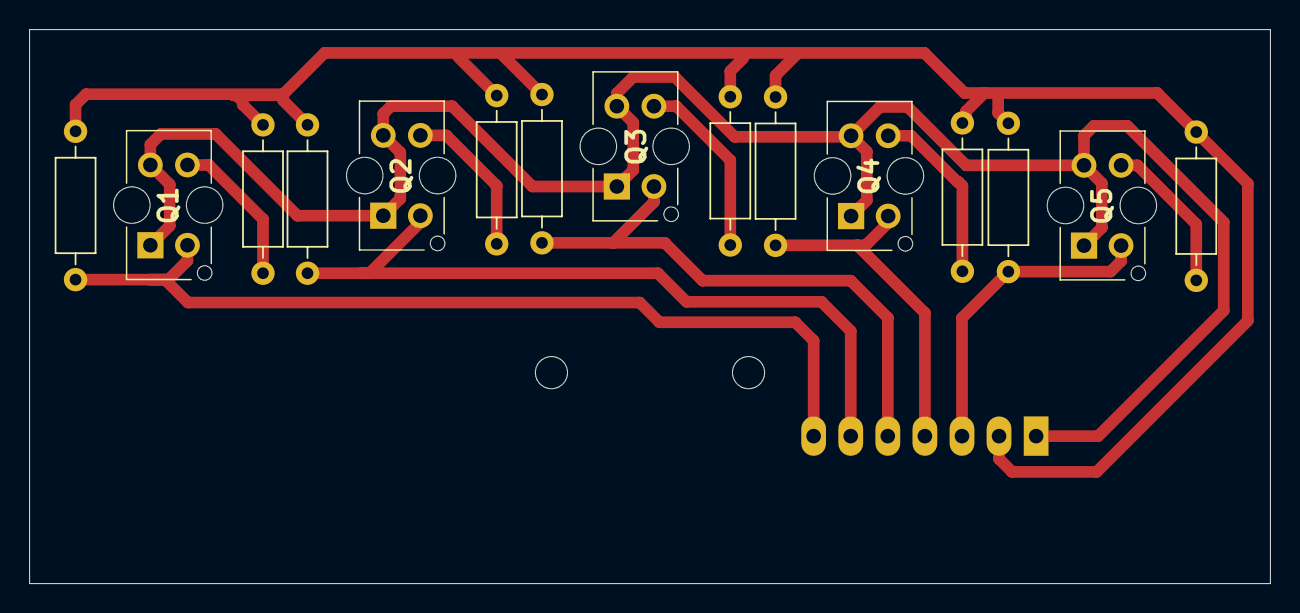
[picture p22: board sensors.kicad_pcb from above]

Board: 2 copper layers, 85.0 x 38.0 mm, 16 parts (1 on the bottom side), 12 nets.

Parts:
J1: Conn_01x07_Pin; PinHeader_1x07_P2.54mm_Horizontal
Q1, Q2, Q3, Q4, Q5: TCRT5000
R1, R2, R3, R4, R5, R6, R7, R8, R9, R10: R; R_Axial_DIN0207_L6.3mm_D2.5mm_P10.16mm_Horizontal

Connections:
+5V: J1.7, Q1.1 (C), Q1.4 (A), Q2.1 (C), Q2.4 (A), Q3.1 (C), Q3.4 (A), Q4.1 (C), Q4.4 (A), Q5.1 (C), Q5.4 (A)
GND: J1.6, R1.2, R2.2, R3.2, R4.2, R5.2, R6.2, R7.2, R8.2, R9.2, R10.2
unnamed: Q1.3 (K), R2.1
unnamed: Q2.3 (K), R4.1
unnamed: Q3.3 (K), R6.1
unnamed: Q4.3 (K), R8.1
unnamed: Q5.3 (K), R10.1
Out_1: J1.1, Q1.2 (E), R1.1
Out_2: J1.2, Q2.2 (E), R3.1
Out_3: J1.3, Q3.2 (E), R5.1
Out_4: J1.4, Q4.2 (E), R7.1
Out_5: J1.5, Q5.2 (E), R9.1

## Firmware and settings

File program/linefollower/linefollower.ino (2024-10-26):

#include "SparkFun_TB6612.h"

#ifndef cbi
#define cbi(sfr, bit) (_SFR_BYTE(sfr) &= ~_BV(bit))
#endif
#ifndef sbi
#define sbi(sfr, bit) (_SFR_BYTE(sfr) |= _BV(bit))
#endif

// Piny do silników
  #define AIN1 7
  #define AIN2 8
  #define PWMA 5
  
  #define BIN1 2
  #define BIN2 1
  #define PWMB 3
  
  #define STBY 4

// Piny do sensorów
#define S1 A0
#define S2 A1
#define S3 A2
#define S4 A3
#define S5 A4

// Pozostałe piny
#define CN A5       //Czujnik napięcia
#define Led1 10     //Przedni led
#define Led2 6      //Tylni led
#define Button 9

// Stałe związane z silnikami 
#define max_speed 100.0 //set Max Speed Value
#define max_speed_change 350 //set Max Speed Change Value

// PID
#define set_point 2000
#define sensor_weight 1000
int minValues[5] = {0,0,0,0,0};
int maxValues[5] = {1023, 1023, 1023, 1023, 1023};
float Kp = 1; //set Kp Value  Optimized: K=0.73 I=0.0007 D=1 max_speed=165
float Ki = 0.000; //set Ki Value
float Kd = 0; //set Kd Value

//aditional const to control error value magnitude
#define silencer 1

#define max_offroad_time 1000
#define delay_time 1

int state = 0;
// Konfiguracja silników
const int offsetA = 1;
const int offsetB = -1;

Motor motor1 = Motor(AIN1, AIN2, PWMA, offsetA, STBY);      //prawy motor
Motor motor2 = Motor(BIN1, BIN2, PWMB, offsetB, STBY);      //lewy motor

const int sensorPins[5] = {S1, S2, S3, S4, S5};
long sensorMults[5] = {0,0,0,0,0};

float volts = 0;
bool robotRunning = false;
bool lastSwitchState = HIGH;

// zmienne do PID
long sensors_sum=0;
long sensors_average=0;
long sensors[5]={0,0,0,0,0};

long Position=0;
long proportional=0;
long integral=0;
long derivative=0;
long last_proportional=0;
long error_value=0;

int left_speed=0;
int right_speed=0;

int last_left_speed=0;
int last_right_speed=0;

int offroad_time=0;
bool ifLedOn = false;

void setup() {
  analogReference(DEFAULT);

  sbi(ADCSRA, ADPS2);
  sbi(ADCSRA, ADPS1);
  cbi(ADCSRA, ADPS0);

  for (int i = 0; i < 5; i++) {
    pinMode(sensorPins[i], INPUT);
  }

  pinMode(Led1, OUTPUT);
  pinMode(Led2, OUTPUT);
  pinMode(Button, INPUT_PULLUP);

  for( int i = 0; i < 14; i++){
    if(i == 6 || i == 10) continue;
    pinMode(i , INPUT_PULLUP);
  }
  
  digitalWrite(Led1, LOW);
  digitalWrite(Led2, LOW);
  for (int i = 0; i < 5; i++){
      sensorMults[i] = i * sensor_weight;
      
  }
}

void loop() {
  volts = analogRead(CN) * 10.0 / 1023.0;
   //Poniżej minimalnego napięcia baterii
  if(volts < 7.5){
    // Czy robot jest włączony?
      if(robotRunning){
        robotRunning = false;
        
        Shutdown();
      }

    while(1){
      digitalWrite(Led2, HIGH);
      delay(1000);
      digitalWrite(Led2, LOW);
      delay(1000);
    }
  }else if(volts < 8){
    digitalWrite(Led2, HIGH);
  }else{
    digitalWrite(Led2, LOW);
  }

  bool currentSwitchState = digitalRead(Button);

  if (currentSwitchState == LOW && lastSwitchState == HIGH) {
    robotRunning = !robotRunning;

    if (robotRunning) {
      delay(300);
      currentSwitchState = digitalRead(Button);
      if(currentSwitchState == LOW){
        calibrate();
        robotRunning = !robotRunning;
        }
       else{
      Start();
       }
    } else {
      Shutdown();
    }

    delay(1000);
  }

  lastSwitchState = currentSwitchState;

  if (robotRunning){
    sensors_sum = 0;
    sensors_average = 0;
    
    for (int i = 0; i < 5; i++){
      sensors[i] = process_signal(analogRead(sensorPins[i]));
      sensors_average += sensors[i] * sensorMults[i];
      sensors_sum += sensors[i];
      
    }

    if(sensors_sum < 4500 && sensors_sum > 2500){
      ifLedOn = true;
      digitalWrite(Led1, HIGH);
      offroad_time = 0;
      
      Position = int(sensors_average / sensors_sum);
      pid_calc();
      calc_turn();

       motor_drive(right_speed,left_speed);
    } else {
      if(offroad_time % 100 == 0){
        if(ifLedOn){
          ifLedOn = false;
          digitalWrite(Led1, LOW);
        }else{
          ifLedOn = true;
          digitalWrite(Led1, HIGH);
        }
      }
      if(offroad_time >= max_offroad_time){
        ifLedOn = true;
        digitalWrite(Led1, HIGH);
        robotRunning = false;
        Shutdown();
        offroad_time = 0;
      }else{
        offroad_time += delay_time;
      }
    }



  }

  delay(delay_time);
}

void Shutdown(){
  brake(motor1, motor2);
  delay(1500);

  digitalWrite(STBY, LOW);

  delay(500);
  ifLedOn = false;
  digitalWrite(Led1, LOW);
}
void Start(){
  digitalWrite(STBY, HIGH);

  delay(1000);
  ifLedOn = true;
  digitalWrite(Led1, HIGH);
}
void pid_calc() 
{
  

    proportional=Position-set_point;
    integral = integral + proportional;
    derivative = proportional - last_proportional;
    last_proportional = proportional;
    error_value = long(proportional * Kp + integral * Ki + derivative * Kd);

}
void calc_turn()
{
  //Restricting the error value between +256.
  error_value *= silencer;
  
  if (error_value < -max_speed){
    error_value = -max_speed;
  }
  if (error_value > max_speed){
    error_value = max_speed;
  }

  // If error_value is less than zero calculate right turn speed values
  if (error_value >= 0){
    right_speed = max_speed - error_value;
    left_speed = max_speed;
  } else {
    right_speed = max_speed;
    left_speed = max_speed + error_value;
  }
}
void motor_drive (int right_speed, int left_speed)
{
  if (right_speed > max_speed)  right_speed = max_speed;
  if (right_speed < 0)          right_speed = 0;
  if (left_speed > max_speed)   left_speed = max_speed;
  if (left_speed < 0)           left_speed = 0;

  // ograniczenie przyśpieszenia silników
  double left_speed_cap = last_left_speed + max_speed_change;
  double right_speed_cap = last_right_speed + max_speed_change;

  if(max_speed < left_speed_cap)    left_speed_cap = max_speed;
  if(max_speed < right_speed_cap)   right_speed_cap = max_speed;
  
  if (left_speed_cap < left_speed)    left_speed = left_speed * (left_speed_cap/max_speed);
  if (right_speed_cap < right_speed)  right_speed = right_speed * (right_speed_cap/max_speed);
  
  if(left_speed <= 5){
    motor2.drive(5);
    last_left_speed = 5;
  }else{
    motor2.drive(left_speed);
    last_left_speed = left_speed;
  }

  if(right_speed <= 5){
    motor1.drive(5);
    last_right_speed = 5;
  }else{
    motor1.drive(right_speed);
    last_right_speed = right_speed;
  }
}

  void calibrate() {
    state = (state + 1) % 3;
    switch (state){
      case 0:
        break;
       case 1:
        break;
       case 2:
        break;
    }

}

int process_signal(int x){

  if(x < 380){
    return 0;
  }
  if (x > 680){
    return 1000;
  }
  return x;
}
